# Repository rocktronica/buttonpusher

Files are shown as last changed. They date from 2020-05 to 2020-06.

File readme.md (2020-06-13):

# buttonpusher

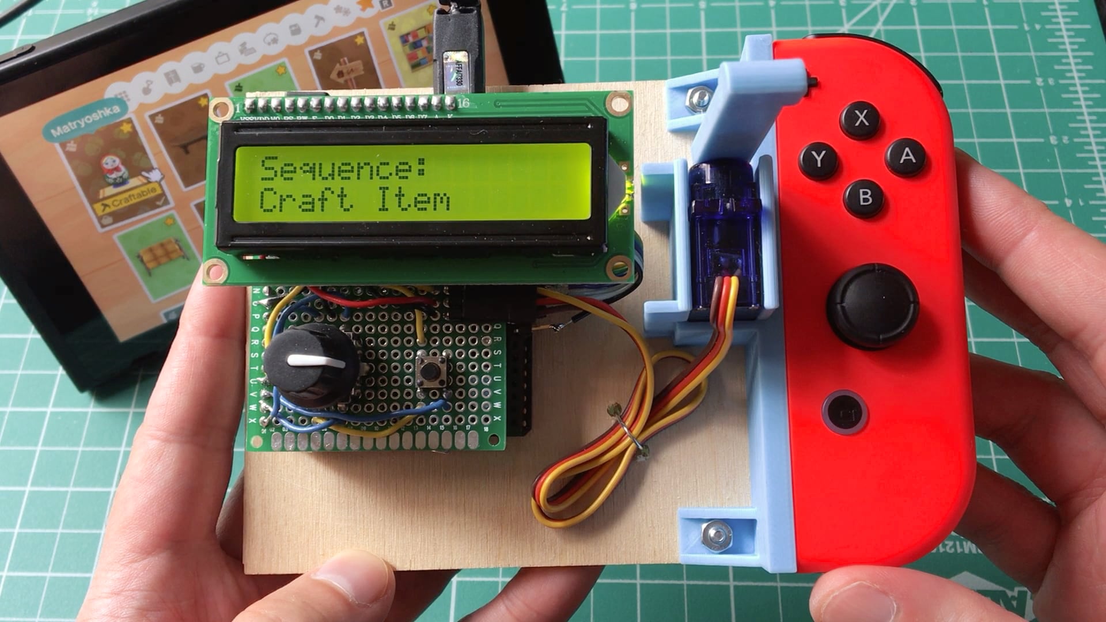
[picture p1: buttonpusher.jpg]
buttonpusher


This "buttonpusher" is a 3D-printed machine that, you guessed it!, pushes the "A" button of a Nintendo Joy-Con Switch at pre-programmed sequences for variable number of times.

buttonpusher is 3D-printed and made from off-the-shelf electronics from Adafruit. It requires no modifications to the Nintendo gear.

**Blog post:** [https://blog.tommy.sh/posts/buttonpusher/](https://blog.tommy.sh/posts/buttonpusher/)  
**Video:** [https://vimeo.com/427842316](https://vimeo.com/427842316)

## Sequences

I made this specifically for Animal Crossing, where you sometimes need to [craft a whole bunch of something](https://animalcrossing.fandom.com/wiki/DIY_recipes) and it takes a long time and is super boring... but it could be easily extended for other games or usages, as long as the only button required to push is "A" and the sequence timing is fixed!

Here's what's baked in currently:

* **Craft Item**: craft an item at a DIY workbench
* **Purchase Item**: buy an item at Nook's Cranny
* **Bell Voucher**: exchange Nook Miles for Bell Vouchers at the [Nook Stop terminal](https://animalcrossing.fandom.com/wiki/Nook_Stop)
* **Wish on Stars for 1 Minute**: for use during a [meteor shower](https://animalcrossing.fandom.com/wiki/Meteor_shower)
* **Debug**: ...for testing!

## Make Your Own

### Parts

This repo has the CircuitPython code used for the microcontroller, the 3D-printed models, as well as the OpenSCAD code used to make those models.

Beyond that, you will need:

* [Micro servo](https://www.adafruit.com/product/169)
* [Adafruit Metro M0 Express](https://www.adafruit.com/product/3505) (or a similar microcontroller)
* Character LCD (I used [this](https://www.jameco.com/shop/ProductDisplay?catalogId=10001&langId=-1&storeId=10001&productId=2295423) but any 16x2 should work great)
* [Rotary encoder w/ button](https://www.adafruit.com/product/377) to select the sequence and the number of times to run it
* Tactile button to cancel sequence
* Potentiometer to adjust LCD contrast

### Fritzing Circuit

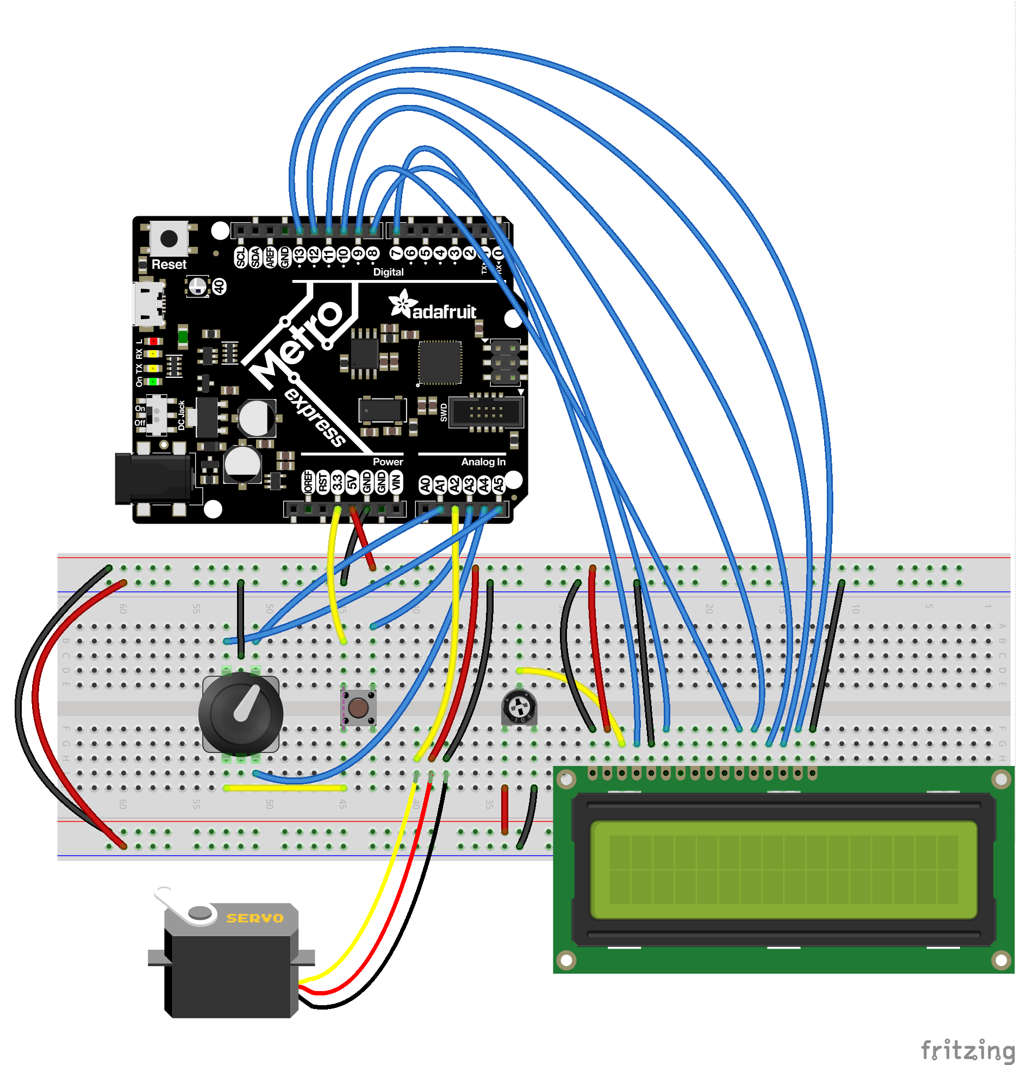
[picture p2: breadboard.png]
buttonpusher circuit in Fritzing


### Deployment

Unlike regular CircuitPython projects, the `.py` files here need to be compiled into `.mpy` with [mpy-cross](https://learn.adafruit.com/building-circuitpython/build-circuitpython) before being copied over. Without that, memory on the board is quickly exhausted.

Once that's done, copy `main.py` and the `lib` folder onto the device over USB.

### Assembly

1. Insert servo into its mounting cavity -- it should fit snugly and won't need its screws
2. Attach the one-sided servo horn into the 3D-printed hammer arm, and attach that to the servo axle
3. Optionally, use machine screws to mount everything together
4. Slide Joy-Con into mount

### Usage

Once everything is installed and the circuit is assembled:

1. Turn rotary encoder to cycle through sequences
2. Press rotary encoder _in_ to confirm selection
3. Do the same to select the count of times to run sequence
4. Use tactile button to cancel sequence or navigate back in menu

## License

MIT License

Copyright (c) 2020

Permission is hereby granted, free of charge, to any person obtaining a copy
of this software and associated documentation files (the "Software"), to deal
in the Software without restriction, including without limitation the rights
to use, copy, modify, merge, publish, distribute, sublicense, and/or sell
copies of the Software, and to permit persons to whom the Software is
furnished to do so, subject to the following conditions:

The above copyright notice and this permission notice shall be included in all
copies or substantial portions of the Software.

THE SOFTWARE IS PROVIDED "AS IS", WITHOUT WARRANTY OF ANY KIND, EXPRESS OR
IMPLIED, INCLUDING BUT NOT LIMITED TO THE WARRANTIES OF MERCHANTABILITY,
FITNESS FOR A PARTICULAR PURPOSE AND NONINFRINGEMENT. IN NO EVENT SHALL THE
AUTHORS OR COPYRIGHT HOLDERS BE LIABLE FOR ANY CLAIM, DAMAGES OR OTHER
LIABILITY, WHETHER IN AN ACTION OF CONTRACT, TORT OR OTHERWISE, ARISING FROM,
OUT OF OR IN CONNECTION WITH THE SOFTWARE OR THE USE OR OTHER DEALINGS IN THE
SOFTWARE.

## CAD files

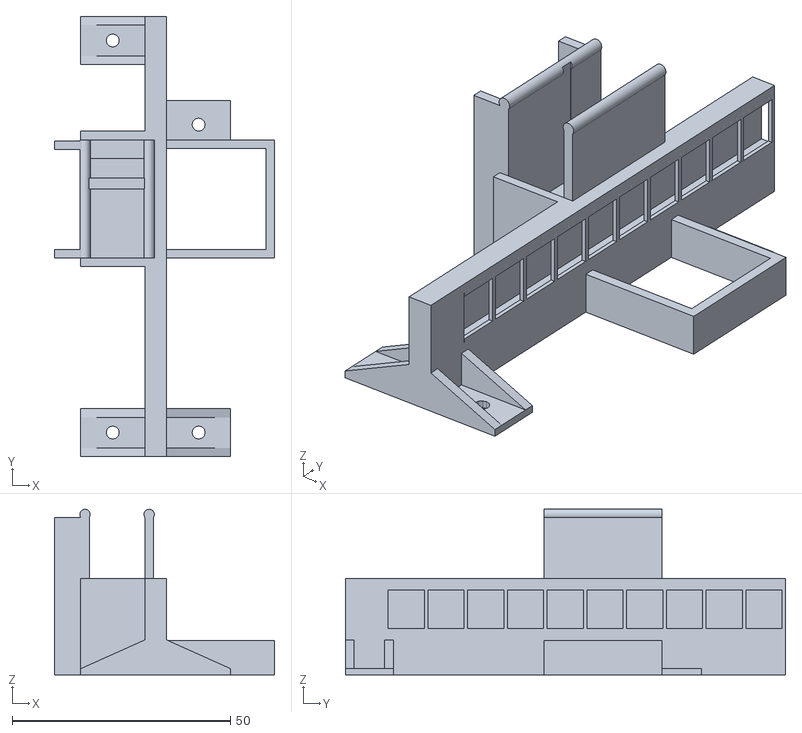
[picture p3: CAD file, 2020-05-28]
3d-models/buttonpusher.stl
50.5 x 100.9 x 38.0

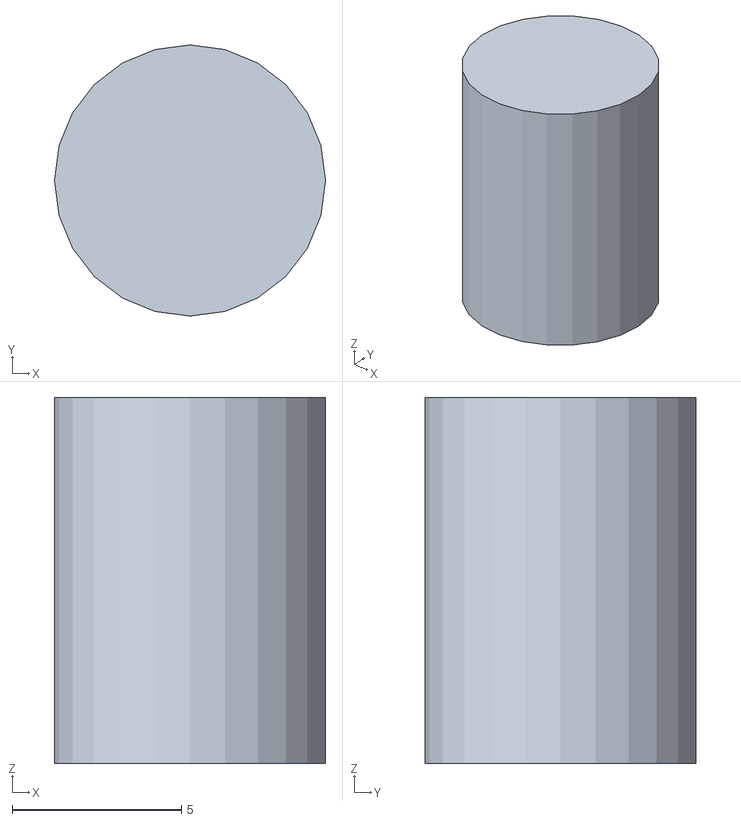
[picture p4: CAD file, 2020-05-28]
3d-models/standoff.stl
8.00 x 8.00 x 10.8

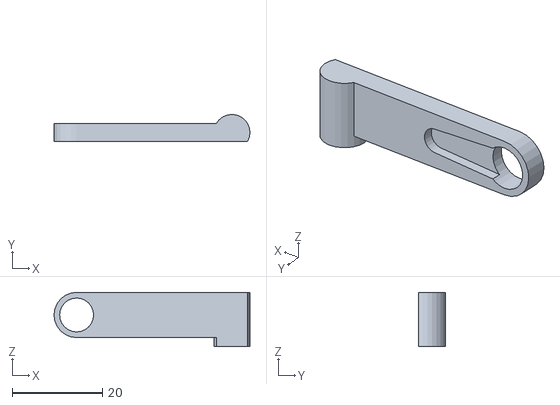
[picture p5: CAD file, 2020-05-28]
3d-models/horn.stl
43.4 x 6.00 x 12.0

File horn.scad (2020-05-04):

module horn(
    width,
    length,
    height,
    clearance,
    cavity_diameter,
    wall,
    button_diameter = 8,
    $fn = 18
) {
    e = .005678;

    module cavity(
        diameter = cavity_diameter,
        shim_count = 3,
        shim_width = 1,
        shim_length = .5,
        _height = length + e * 2
    ) {
        difference() {
            cylinder(
                h = _height,
                d = diameter
            );

            for (i = [0 : shim_count - 1]) {
                rotate([0, 0, i * 360 / shim_count]) {
                    translate([
                        shim_width / -2,
                        diameter / 2 - shim_length,
                        -e
                    ]) {
                        cube([shim_width, shim_length, _height + e * 2]);
                    }
                }
            }
        }
    }

    module armpit(_height = 3) {
        x = height;

        translate([x, -e, -e]) {
            cube([
                width - x - button_diameter,
                length + e * 2,
                _height + e
            ]);
        }
    }

    difference() {
        cube([width, length, height]);
        armpit();
        translate([height / 2, -e, height / 2])
            rotate([-90, 0, 0]) cavity();
    }
}

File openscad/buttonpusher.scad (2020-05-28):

include <lib/mount.scad>;
include <lib/servo.scad>;
include <lib/horns.scad>;
include <lib/animation.scad>;

module buttonpusher(
    horn_width = 20,
    horn_length = SERVO_SHAFT_HEIGHT,
    horn_height = 10,
    horn_clearance = 1,
    horn_angle = 0,

    wall = 2,

    show_peripherals = true,
    show_buttonpusher = true,
    show_horn = true,

    screw_hole_size = 2.8,
    screw_nut_diameter = 7, // w/ wiggle room

    tolerance = .1,
    loose_tolerance = .2,
    $fn = 12
) {
    width = SERVO_LENGTH + wall * 2 + tolerance * 2;

    ZR_BUTTON_STILT = 8;

    JOYCON_WIDTH = 33;
    JOYCON_LENGTH = 101;
    JOYCON_HEIGHT = 14;
    JOYCON_BUTTON_X = 23;
    JOYCON_BUTTON_Y = 75;
    JOYCON_BUTTON_DIAMETER = 8;
    JOYCON_BUTTON_HEIGHT = 2;

    e = .005678;

    servo_x = wall + SERVO_LENGTH / 2;
    servo_y = JOYCON_BUTTON_Y - SERVO_SHAFT_DIAMETER / 2 - SERVO_FULL_HEIGHT;
    servo_z = ZR_BUTTON_STILT + MOUNT_HEIGHT
        + JOYCON_BUTTON_HEIGHT + horn_clearance
        + horn_height / 2;

    horn_y = servo_y + SERVO_FULL_HEIGHT + tolerance;

    servo_tabs_y = servo_y - tolerance;

    module _servo(
        bleed = 0,
        show_fins = true,
        show_shaft = true,
        show_cable = true,
        show_base = true
    ) {
        translate([
            servo_x,
            servo_y,
            servo_z
        ]) rotate([-90, 90, 0]) {
            servo(
                bleed = bleed,
                show_fins = show_fins,
                show_shaft = show_shaft,
                show_cable = show_cable,
                show_base = show_base
            );
        }
    }

    module _horn() {
        translate([
            servo_x + tolerance,
            horn_y + tolerance,
            servo_z
        ]) {
            hammer_horn(
                angle = horn_angle,
                distance = (width - servo_x) + MOUNT_DEPTH + JOYCON_BUTTON_X
                    - tolerance,
                extension = JOYCON_BUTTON_HEIGHT
            );
        }
    }

    module _servo_tabs(
        _width = wall,
        _length = SERVO_FULL_HEIGHT + tolerance * 2,
        _support_width = wall * 3
    ) {
        _height = (servo_z + SERVO_SHAFT_X) + e;

        module _wall() {
            cube([_width, _length, _height]);

            translate([_width / 2, 0, _height + _width / 3]) {
                rotate([-90, 0, 0]) {
                    cylinder(
                        d = _width + tolerance * 4,
                        h = _length,
                        $fn = 24
                    );
                }
            }
        }

        module _side_supports() {
            for (_y = [
                servo_tabs_y,
                servo_tabs_y + SERVO_FULL_HEIGHT - _width
            ]) {
                translate([-_support_width, _y, 0]) {
                    cube([
                        _support_width + e,
                        _width,
                        _height
                    ]);
                }
            }
        }

        difference() {
            union() {
                for (_x = [0, width - _width]) {
                    translate([_x, servo_tabs_y, 0]) {
                        _wall();
                    }
                }

                _side_supports();
            }

            _servo(
                bleed = tolerance,
                show_fins = true,
                show_shaft = false,
                show_cable = false,
                show_base = false
            );
        }
    }

    module _base() {
        module _stool(
            _width = JOYCON_WIDTH * .75,
            _length = SERVO_FULL_HEIGHT + tolerance * 2,
            _height = ZR_BUTTON_STILT - tolerance * 1
        ) {
            translate([width + MOUNT_DEPTH - e, servo_tabs_y - e, 0]) {
                difference() {
                    cube([_width + e, _length, _height]);

                    translate([-e, wall, -e]) {
                        cube([
                            _width - wall + e,
                            _length - wall * 2,
                            _height + e * 2
                        ]);
                    }
                }
            }
        }

        difference() {
            union() {
                translate([0, servo_y - wall, 0]) {
                    cube([
                        width,
                        SERVO_FULL_HEIGHT + tolerance * 2 + wall * 2,
                        ZR_BUTTON_STILT + MOUNT_HEIGHT
                    ]);
                }

                translate([width - wall, 0, 0]) {
                    cube([wall + e, MOUNT_LENGTH, ZR_BUTTON_STILT + MOUNT_HEIGHT]);
                }

                translate([width, 0, 0]) {
                    cube([MOUNT_DEPTH, MOUNT_LENGTH, ZR_BUTTON_STILT + e]);
                }
            }

            _servo(bleed = tolerance);
        }

        _stool();
    }

    module _screw_mounts(
        _width = width - wall,
        _length = screw_nut_diameter + 4,
        _height = ZR_BUTTON_STILT - e, // no overlap to avoid STL errors
        _base_height = 1.4
    ) {
        LEFT = "left";
        RIGHT = "right";

        module _screw_mount(placement) {
            difference() {
                hull() {
                    if (placement == LEFT) {
                        translate([_width, 0, _height - e]) {
                            cube([e, _length, e]);
                        }
                    } else if (placement == RIGHT) {
                        translate([-e, 0, _height - e]) {
                            cube([e, _length, e]);
                        }
                    }

                    cube([_width, _length, _base_height]);
                }

                translate([_width / 2, _length / 2, -e]) {
                    cylinder(
                        d = screw_hole_size + tolerance * 2,
                        h = _base_height + e * 2
                    );
                }

                if (placement) {
                    translate([-e, wall, _base_height]) {
                        cube([
                            _width + e * 2,
                            _length - wall * 2,
                            _height - _base_height + e
                        ]);
                    }
                }
            }
        }

        for (xyp = [
            [e, 0, LEFT],
            [e, MOUNT_LENGTH - _length, LEFT],
            [width + MOUNT_DEPTH - e, 0, RIGHT],
            [width + MOUNT_DEPTH - e, servo_tabs_y + SERVO_FULL_HEIGHT - wall + tolerance * 2],
        ]) {
            translate([xyp[0], xyp[1], 0]) {
                _screw_mount(xyp[2]);
            }
        }
    }

    if (show_horn) {
        _horn();
    }

    if (show_buttonpusher) {
        _screw_mounts();
        _servo_tabs();
        _base();
        translate([width, 0, ZR_BUTTON_STILT]) {
            mount(MOUNT_DEPTH, fdm = true, tolerance = loose_tolerance);
        }
    }

    # if (show_peripherals) {
        translate([tolerance, 0, 0]) _servo();

        translate([width + MOUNT_DEPTH - e, 0, ZR_BUTTON_STILT]) {
            cube([
                JOYCON_WIDTH,
                JOYCON_LENGTH,
                JOYCON_HEIGHT
            ]);

            translate([JOYCON_BUTTON_X , JOYCON_BUTTON_Y, JOYCON_HEIGHT]) {
                cylinder(
                    d = JOYCON_BUTTON_DIAMETER,
                    h = JOYCON_BUTTON_HEIGHT
                );
            }
        }
    }
}

/* Constants pulled out to be overwritten by make_stls.sh */
SHOW_PERIPHERALS = true;
SHOW_BUTTONPUSHER = true;
SHOW_HORN = true;

buttonpusher(
    show_peripherals = SHOW_PERIPHERALS,
    show_buttonpusher = SHOW_BUTTONPUSHER,
    show_horn = SHOW_HORN,
    horn_angle = 90 * ease_in_out_quad(undulate($t))
);

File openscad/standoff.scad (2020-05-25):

module glued_standoff(
    height = 10.8,
    diameter = 8,
    $fn = 24
) {
    cylinder(h = height, d = diameter);
}

glued_standoff();

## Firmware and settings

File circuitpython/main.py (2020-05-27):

from time import monotonic
from utils import get_seconds_to_wait
from wait import Wait
import board

from button import Button
from display import Display
from hammer import Hammer
from menu import Menu
from sequences import SEQUENCES

RUN_COUNT_MAX = 120

cancel_button = Button(board.A3)
confirm_button = Button(board.A4)

display = Display(
    pin_lcd_rs=board.D7,  # pin 4 on LCD
    pin_lcd_en=board.D8,  # pin 6 on LCD
    pin_lcd_d7=board.D12,  # pin 14 on LCD
    pin_lcd_d6=board.D11,  # pin 13 on LCD
    pin_lcd_d5=board.D10,  # pin 12 on LCD
    pin_lcd_d4=board.D9,  # pin 11 on LCD
    pin_lcd_backlight=board.D13,  # 15
)
wait = Wait(confirm_button, cancel_button)
hammer = Hammer(board.A2, wait)
menu = Menu(board.A1, board.A5, confirm_button, cancel_button, display)


def run(sequence, count=0):
    hammer.rest()
    halt = False

    display.start_sequence(sequence, count)

    start_time = monotonic()

    def get_seconds_elapsed():
        return monotonic() - start_time

    def update_display():
        display.set_seconds_elapsed(get_seconds_elapsed())

    for item_index in range(0, count, 1):
        if halt:
            break

        display.start_item(item_index)

        for (step_index, _) in enumerate(sequence):
            display.start_step(step_index)

            halt = wait.interruptible_sleep(
                get_seconds_to_wait(
                    item_index, step_index, sequence, get_seconds_elapsed()
                ),
                update_display,
            )
            if halt:
                break

            hammer.click()

    display.print("Stopped." if halt else "All done!")
    hammer.default()

    wait.idle(5)


while True:
    hammer.default()

    sequence_i = 0
    count_i = 0
    run_count = None
    while run_count is None:
        (_, sequence_i) = menu.choice(
            "Sequence",
            list(map(lambda seq: seq.get("text"), SEQUENCES)),
            default_selected_index=sequence_i,
        )
        (run_count, count_i) = menu.choice(
            "Count",
            range(1, RUN_COUNT_MAX + 1, 1),
            is_cancelable=True,
            default_selected_index=count_i,
        )

    run(SEQUENCES[sequence_i].get("value"), run_count)

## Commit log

2020-04-14 Blink LED
2020-04-17 Fix PWM frequency
    50 was the original value from the example code, but I lowered it
    while debugging the old range code. Seems better now.
    [main.py]
2020-04-21 Fine-tune
    Moved servo POWER to USB instead of 3v for more umph, requiring some
    changes to PWM freq and PRESSED angle (stronger push = lesser angle)
2020-04-28 Add (untested!) mount
    [mount.scad]
2020-04-28 Tidy mount() interface
    [mount.scad]
2020-04-29 Experiment with mount FDM
    [mount.scad]
2020-05-01 Fix MOUNT_STOP
    Was measuring from wrong part
    [mount.scad]
2020-05-01 Temporarily decouple tolerances for finer tests
    [mount.scad]
2020-05-01 Expose supports count for lips
    [mount.scad]
2020-05-01 Narrow tolerance test to mount_lip_beyond_wall...
    And narrow width for tests too
    [mount.scad]
2020-05-01 Start servo.scad
    [servo.scad]
2020-05-01 Update MOUNT_LIP_BEYOND_WALL
    [mount.scad]
2020-05-01 Couple tolerances
    [mount.scad]
2020-05-01 Derive mount supports count based on FDM best practices
    [mount.scad]
2020-05-02 Start buttonpusher.scad
    [buttonpusher.scad, mount.scad, servo.scad]
2020-05-02 Add forgotten tolerance to mount
    [buttonpusher.scad]
2020-05-02 Rotate servo
    [buttonpusher.scad]
2020-05-03 Start horn
    [buttonpusher.scad, servo.scad]
2020-05-03 Test horn fit
    [buttonpusher.scad]
2020-05-03 fixup! start horn
    [buttonpusher.scad]
2020-05-03 Refine arm w/ fit test result
    [buttonpusher.scad]
2020-05-03 Debug servo angles
2020-05-03 Refine servo angles
    Servo doesn't have near enough torque for these angles to work.
    Gonna need to make a lever.
    [main.py]
2020-05-04 Extract horn
    [buttonpusher.scad, horn.scad]
2020-05-05 Whoops, fix unused SERVO consts
    [servo.scad]
2020-05-05 Start lever design
    Servo isn't strong enough push button down, so trying a lever to
    increase mechanical advantage
    [buttonpusher.scad]
2020-05-05 Tidy mount support preview
    [mount.scad]
2020-05-05 Run a plank through controller and servo mounts
    The plank is some hobby craft wood I had laying around.
    The goal is to do this to figure out the lever and its placement
    manually before coding them into the design.
    [buttonpusher.scad]
2020-05-05 Deal with servo cable
    [servo.scad]
2020-05-05 Update beam width and axle cavity
    [buttonpusher.scad]
2020-05-05 Rename horn -> horns file
    [buttonpusher.scad, horns.scad]
2020-05-06 More refinements
    Messy! YOLO
    [buttonpusher.scad, horns.scad]
2020-05-07 Try a horn that screws in
    [horns.scad]
2020-05-07 Servo shaft pushes in, so fix its measurement
    [servo.scad]
2020-05-07 Revise screw_horn
    * Narrow top profile so it aligns correctly
    * Fix cavity that was too tall
    * Try shims
    [horns.scad]
2020-05-07 Ditch lever for screw_horn
    This partially reverts commit 5a54c2a9693e11d5559e802ba00e362c7329adb3.
    [buttonpusher.scad, horns.scad]
2020-05-07 Don't require horn cavity shims
    [horns.scad]
2020-05-07 Model stock horn for cavity
    [horns.scad]
2020-05-08 Try stock horn cavity
    [horns.scad]
2020-05-08 Perfect screw_horn, -> hammer_horn
    [buttonpusher.scad, horns.scad]
2020-05-08 Fix missing servo cavity in base
    [buttonpusher.scad]
2020-05-08 Visualize joycon
    [buttonpusher.scad]
2020-05-08 Ditch servo mount for tabs
    [buttonpusher.scad, horns.scad, servo.scad]
2020-05-09 Parameterize visualizing peripherals, not just joycon
    [buttonpusher.scad]
2020-05-09 Narrow base to servo and joycon support
    [buttonpusher.scad]
2020-05-09 Parameterize horn angle
    [horns.scad]
2020-05-09 Hang horn down when resting
    [buttonpusher.scad]
2020-05-09 Update servo angles again
2020-05-09 Eh, the servo only has 180deg of rotation :(
    Revert "Hang horn down when resting"
    This reverts commit d6c401246cf485a4a41a610d96fd6ce60040edf3.
    [buttonpusher.scad]
2020-05-11 Support left servo wall
    The mount wall is too flimsy and bends under pressure. Hopefully
    this does somthing good.
    [buttonpusher.scad]
2020-05-11 Deal with little base thing around servo axle
    Should make for truer fit on servo mount and remove dead space
    [buttonpusher.scad, servo.scad]
2020-05-11 Fix servo centering translation
    [servo.scad]
2020-05-11 Try tighter default tolerance for servo
    [buttonpusher.scad]
2020-05-12 Redesign joycon stool and increase MOUNT_HEIGHT
    Should make it easier to slide in?
    [buttonpusher.scad, mount.scad]
2020-05-12 Readjust PRESSED angle after adding servo support walls
2020-05-12 Animate arm rotation, for fun!
    [animation.scad, buttonpusher.scad]
2020-05-13 Go back to default servo angle at end of sequence
2020-05-14 Organize pin and angle consts
    I'm sure there's a better way to do this
2020-05-15 Use rotary encoder for sequence and count!!
2020-05-15 Ditch superflous PIN enum class
2020-05-15 Abstract all print() and formatting logic to Display class
2020-05-15 Move rotary_encoder from GND to 3v
2020-05-15 Allow sequence sleep to be interrupted
2020-05-15 Fix errant missed setAngle() and deter future mistakes
    [main.py]
2020-05-15 Move button stuff into Button class
2020-05-15 Tidy Button reset logic
    [main.py]
2020-05-16 Extract Button
2020-05-16 Fix errant global display assumption
    [main.py]
2020-05-16 Switch from ItsyBitsy M4 Exp to Metro M0 Exp
    Just pin changes here, nothing functional
    Need a beefier board for some other stuf...
2020-05-17 Fix MemoryError bug by ditching step descriptions
    Previously, with addition of character LCD, was running out of memory,
    and simplifying sequence step to tuple was close but not enough.
    Being that the 16x2 LCD won't even have the real estate to display the
    description text anyway, ditching it seems fine.
    [main.py]
2020-05-18 Add callback arg to interruptible_sleep
    and slow down increment
2020-05-19 Derive step wait times from elapsed time
    Updating the % completion math to use real, elapsed time (instead of
    theoretical, expected time) exposed that the two were out of sync --
    like, runs would finish at 74% or something wacky!
    This change brings them closer together by deriving how long to wait
    on each step (effectively "how much time should have passed at start
    of next step" minus "how much time has passed right now") before
    hammering.
    Funny enough, I think based on interruptible_sleep's increment, the %
    math can be slightly optimistic (like 101% or 102% on short runs), so
    it's always rounded down and capped at 100
    Whew! :sweat_smile:
    [main.py]
2020-05-23 Add pin # comments for LCD module
2020-05-23 Try some screw mounts to hold joycon mount + servo to separate board
    [buttonpusher.scad]
2020-05-24 Reverse rotary encoder pins
    [main.py]
2020-05-25 Git add crude glue standoff
    [standoff.scad]
2020-05-25 Decrease risk of print support failure on joycon mount
    Had one print failure out of the half dozen or so prints, so increasing
    the support length just a smidge to hopefully keep thta to a minimum.
    [mount.scad]
2020-05-25 Swap screw mount nut holes for rectangular locks
    [buttonpusher.scad]
2020-05-25 Prevent screw mount from colliding w/ ZR button
    [buttonpusher.scad]
2020-05-25 Minimize screw mount base and fix STL error
    [buttonpusher.scad]
2020-05-25 Try to preempt some other STL errors
    Looking at the output render makes me realize there are plenty of
    unions that aren't explicit. This fixes a few...
    [buttonpusher.scad]
2020-05-27 Blacken and (mostly) pylint python
    .pylintrc from Adafruit_Learning_System_Guides
    It and Black disagree on bad-continuation, which is annoying. I'm
    deferring to Black for now, since it can auto-fix.
    [main.py]
2020-05-28 Tidy SCAD
    Certainly not exhaustive, but:
    * make _private_module convention consistent
    * properly nest some rotate/translate
    * remove unused horn modules
    [buttonpusher.scad, horns.scad, mount.scad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]
2020-05-28 Separate openscad and circtuitpython code
    [animation.scad, buttonpusher.scad, horns.scad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]
2020-05-28 Move openscad lib code into a folder too
    [buttonpusher.scad]
2020-05-28 Add 3D-model exports
    * Expose SHOW_... constants to CLI
    * Quick lil bash script to use ^
    * New 3d-models folder w/ output from ^
    [buttonpusher.scad, buttonpusher.stl, horn.stl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]
